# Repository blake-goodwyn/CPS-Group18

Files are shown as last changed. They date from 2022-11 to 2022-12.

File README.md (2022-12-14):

# CPS-Group18

## Overview

This is a repository for all development data regarding Group 18's work toward the Cyberphysical Systems module of the Imperial College London's Innovation Design Engineering (IDE) programme. The scope of this project is a 3-week design sprint aimed at a project of the students' choosing - in this case, developing a scale-model, soft-shelled Mars habitat structure that adjusts to aerodynamic shapes based on extreme wind patterns.  

The project team consists of:
- Abigail Hoover
- Richard Alexandre
- Richard "Blake" Goodwyn

## Working with these files

It is suggested that, due to the mechanism of how SolidWorks files are saved, anyone looking to work with the CAD files located in this repo either:
- place this repo at the C:/ location of their local machine
- open and re-save all SolidWorks once their environment has located the new file directory

This is an unfortunate side effect of mixing SolidWorks and Git, whereas an SVN system may be more appropriate. However, due to the fast-paced nature of this project and mixed media of its digital assets, GitHub seemed a reasonable solution for tracking development and hosting a final set of files.

## Mechanical Overview 
### (Refer to /cad folder)

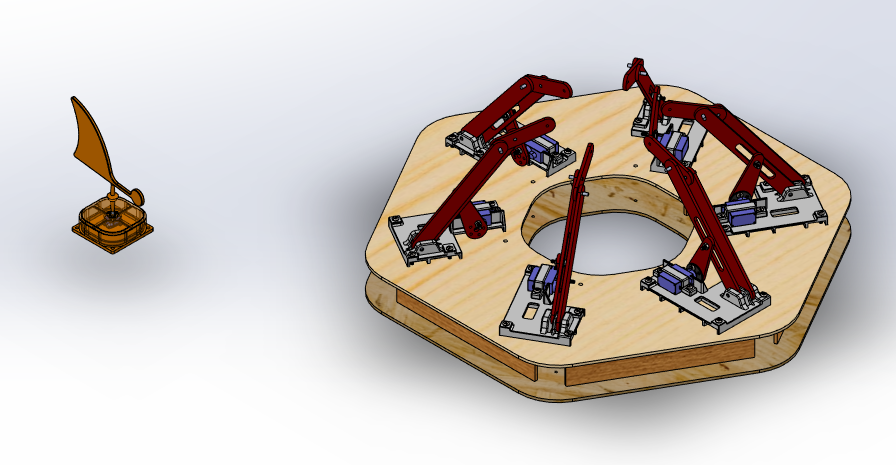
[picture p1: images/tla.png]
Top Level Assembly


The mechanical design of the structure consists of six mechanical arms spaced equally about the structure. Each one consists of a carefully developed 4-bar linkage system driven by a servo arm. The servo arm has a roller that is situated into a slot in a driving link and drives the tip of each arm up-and-down given the servo's position.

The mechanical design in this repo utilizes a top-down design ideology call **master modeling** to form all of the parts. Thus, the mechanical design is driven by three central files:
- *master.prt*, which contains critical assembly level design information like the structure's height and footprint
- *_submaster_linkage_module_4bar.prt*, which contains the critical design information for the assembly of each linkage module
- *_submaster_wind_vane.prt*, which contains the critical design information for the wind vane sub-assembly.

For more information on master modeling, you can refer to [this article from GoEngineer](https://www.goengineer.com/blog/solidworks-tutorial-master-modeling-technique).

## Software Overview
### (Refer to arduino_code)

Our software design utilises two core scripts in addition to a machine learning model to achieve its function: 
- an Arduino script (/arduino_code/MASTER_CODE/master_code) that handles motion of servos, packaging sensor inputs for the Wekinator module, 
and an interprets the feedback from the machine learning module
- a Processing script (machine_learning/master_processing_script/master_rx_tx_script) that takes in the analog sensor values from the Serial port and passes them to a Wekinator module
- a Wekinator machine learning module (machine_learning/final_ML_model/Finalized_ASH_ML_Model) that takes in 2 inputs in the form of float values and gives one integer output that denotes the class output of the model

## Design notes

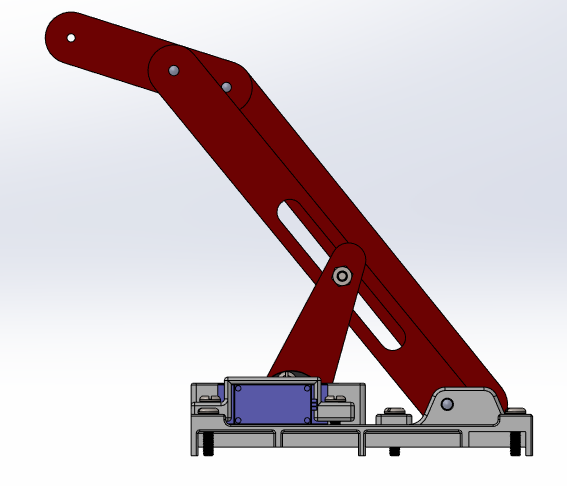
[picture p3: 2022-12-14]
images/linkage_subassy_right.png

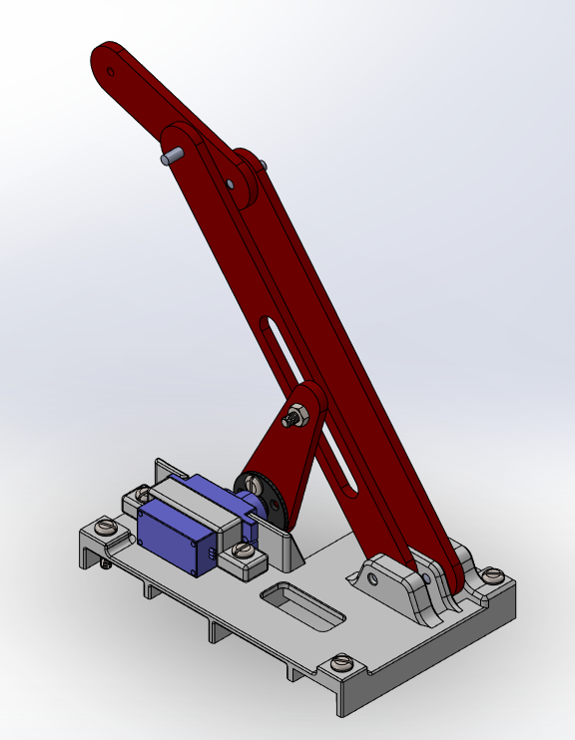
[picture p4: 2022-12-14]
images/linkage_subassy.png

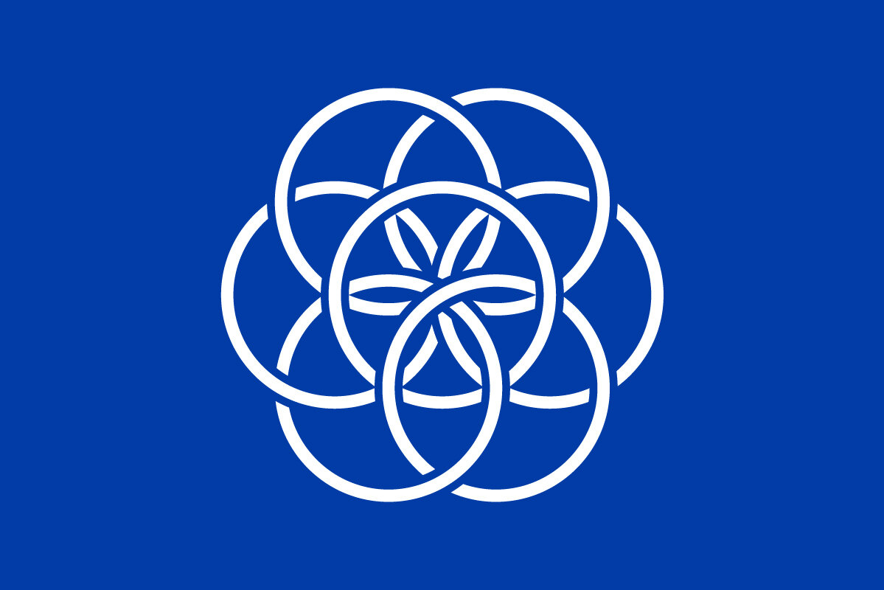
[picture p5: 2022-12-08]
images/EarthFlag.png

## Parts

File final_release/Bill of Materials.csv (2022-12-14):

PART NAME | QTY. | PROCESS | MATERIAL | VENDOR | SUPPLIER P/N | LINK | NOTES
windvane_housing | 1 | PRINT | PRUSA, 0.15MM PLA
wind_vane | 1 | PRINT | PRUSA, 0.15MM PLA
magnet_bracket | 1 | PRINT | PRUSA, 0.15MM PLA
pin_3mm_diam_12mm_length | 25 | PURCHASED | --- | RS COMPONENTS | 270-552 | https://uk.rs-online.com/web/p/dowel-pins/270552
round_bar_magnet | 1 | PURCHASED | --- | RS COMPONENTS | 536-1726 | https://uk.rs-online.com/web/p/magnets/5361726
wind_vane_base | 1 | PRINT | PRUSA, 0.15MM PLA
hall_effect_sensor_honeywell_SS495A | 2 | PURCHASED | --- | RS COMPONENTS | 216-6231 | https://uk.rs-online.com/web/p/hall-effect-sensors/2166231
washer_M3 | 13 | PURCHASED | --- | (STANDARD COMPONENT)
link1 | 6 | CUT | MDF, 3MM THK
link2 | 6 | CUT | MDF, 3MM THK
link3_slotted | 6 | CUT | MDF, 3MM THK
link4_servo_arm | 6 | CUT | MDF, 3MM THK
_mco_roller_link | 6 | PRINT | PRUSA, 0.15MM PLA
sg90 micro servo | 6 | PURCHASED | --- | Feetech | FS90MG
sg90_servo_wheel | 6 | PURCHASED | --- |  |  |  | (included with Feetech FS90MG)
servo_clamp | 6 | PRINT | PRUSA, 0.15MM PLA
servo_plate | 6 | PRINT | PRUSA, 0.15MM PLA
91200A118_18-8 Stainless Steel Pan Head Slotted Screw | 72 | PURCHASED | --- | (STANDARD COMPONENT) |  | https://www.mcmaster.com/91200A118/
91828A211_18-8 Stainless Steel Hex Nut | 48 | PURCHASED | --- | (STANDARD COMPONENT) |  | https://www.mcmaster.com/91828A211/
_new_base_top | 1 | CUT | MDF, 3MM THK
_new_base_bottom | 1 | CUT | MDF, 3MM THK
base_plate_rib | 6 | CUT | MDF, 3MM THK
base_plate_rib_outer | 6 | CUT | MDF, 3MM THK

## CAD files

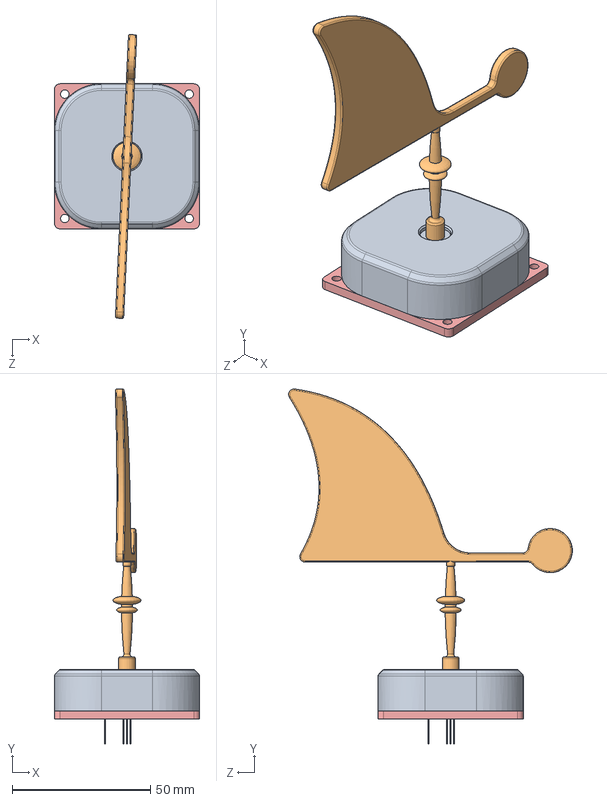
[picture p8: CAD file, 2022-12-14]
cad/_subassy_windvane.SLDASM
52.5 x 128.4 x 102.7 mm
windvane_housing
wind_vane
pin_3mm_diam_12mm_length
round_bar_magnet
wind_vane_base
hall_effect_sensor_honeywell_SS495A x 2
washer_M3

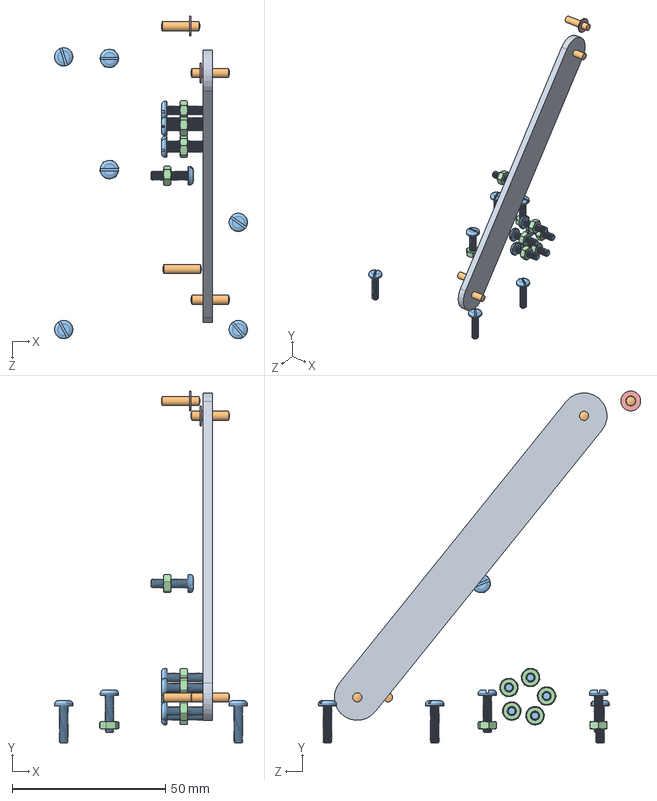
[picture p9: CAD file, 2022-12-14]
final_release/CAD/_subassy_linkage_module.SLDASM
63.0 x 114.9 x 105.3 mm
link1
pin_3mm_diam_12mm_length x 4
91200A118_18-8 Stainless Steel Pan Head Slotted Screws x 12
91828A211_18-8 Stainless Steel Hex Nut x 8
washer_M3 x 2

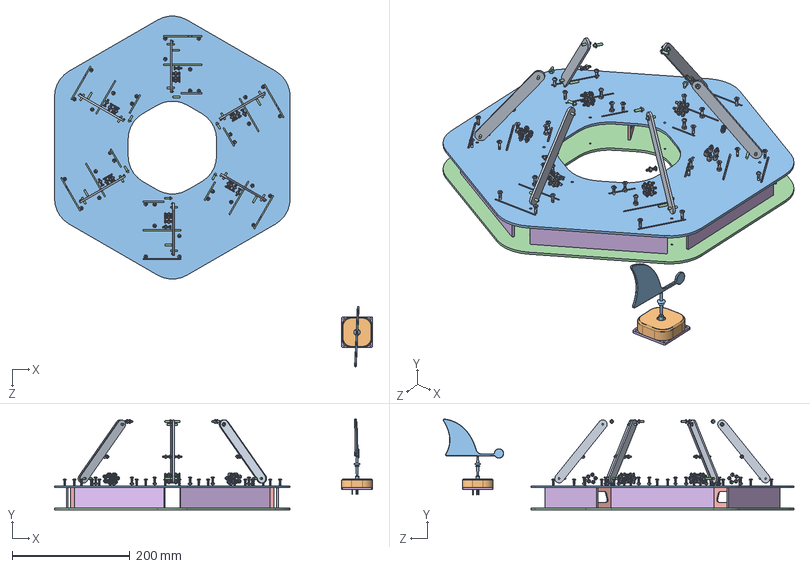
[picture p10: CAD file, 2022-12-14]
cad/_tla.SLDASM
539.6 x 154.4 x 595.0 mm
windvane_housing
wind_vane
pin_3mm_diam_12mm_length x 25
round_bar_magnet
wind_vane_base
hall_effect_sensor_honeywell_SS495A x 2
washer_M3 x 13
link1 x 6
91200A118_18-8 Stainless Steel Pan Head Slotted Screws x 72
91828A211_18-8 Stainless Steel Hex Nut x 48
_new_base_top
_new_base_bottom
base_plate_rib x 6
base_plate_rib_outer x 6

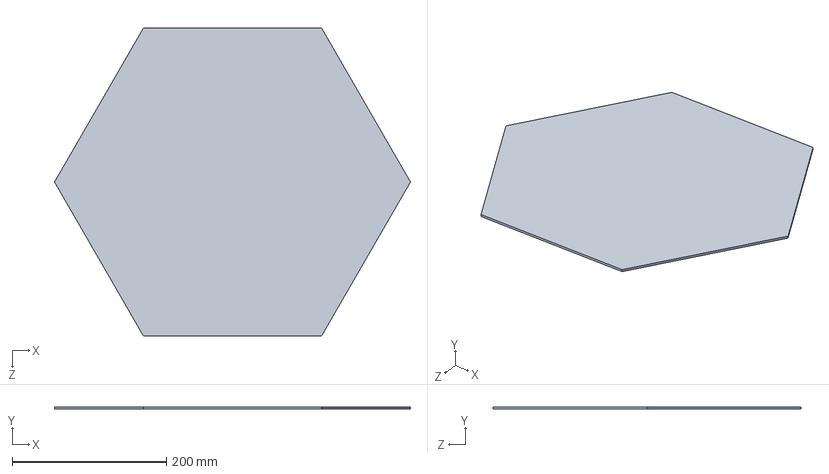
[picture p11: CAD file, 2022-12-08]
cad/_subassy_hexa_base.SLDASM
461.9 x 3.00 x 400.0 mm

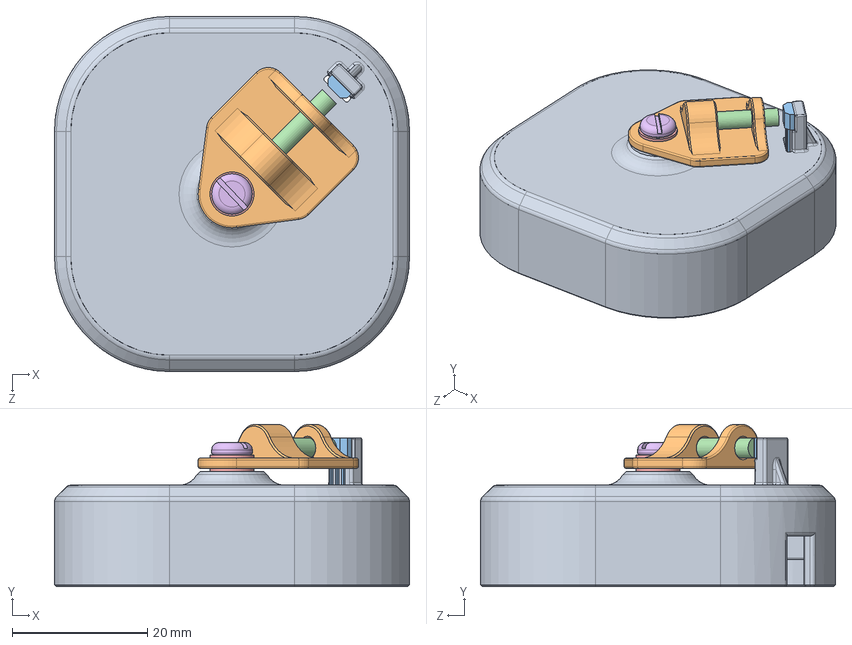
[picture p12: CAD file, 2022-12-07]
cad/_subassy_proto_windvane.SLDASM
52.5 x 24.0 x 52.5 mm
windvane_proto_housing
proto_accelerometer_plate
hall_effect_sensor_honeywell_SS495A
round_bar_magnet
washer_M3 x 3
91200A118_18-8 Stainless Steel Pan Head Slotted Screws
91828A211_18-8 Stainless Steel Hex Nut

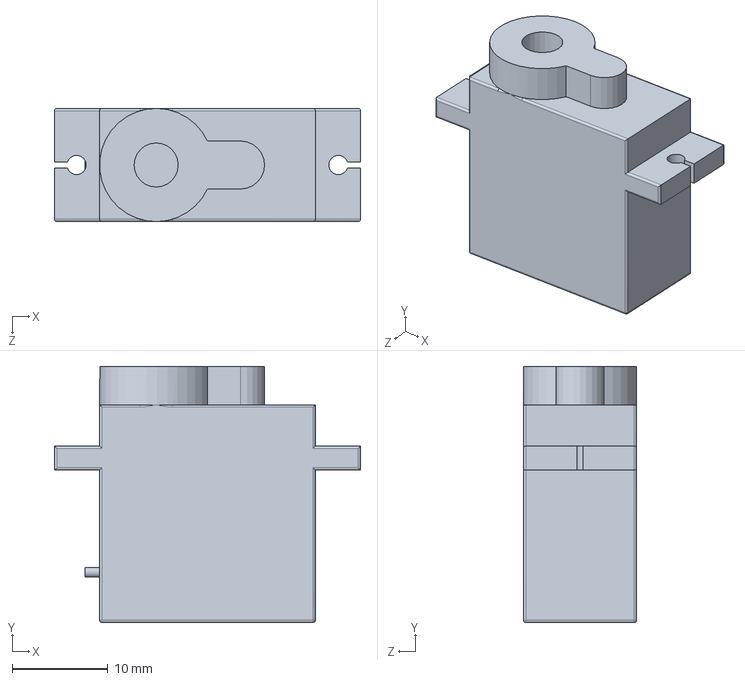
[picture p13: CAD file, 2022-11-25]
arduino_code/sg90-micro-servomotor-1.snapshot.2/Part1.SLDPRT
31.9 x 26.7 x 11.8 mm

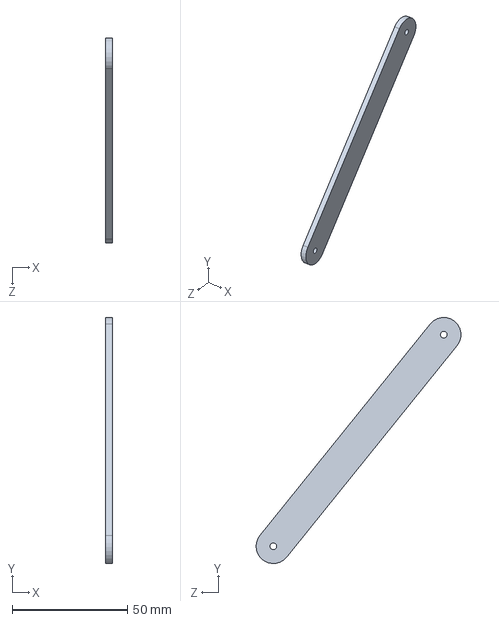
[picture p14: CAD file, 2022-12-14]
final_release/CAD/link1.SLDPRT
3.00 x 106.8 x 89.0 mm

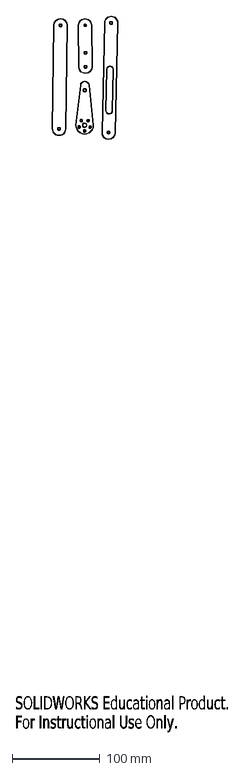
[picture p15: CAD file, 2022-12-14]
final_release/CUT/linkage_4bar_links_1set.DXF
SOLIDWORKS Educational Product.
For Instructional Use Only.

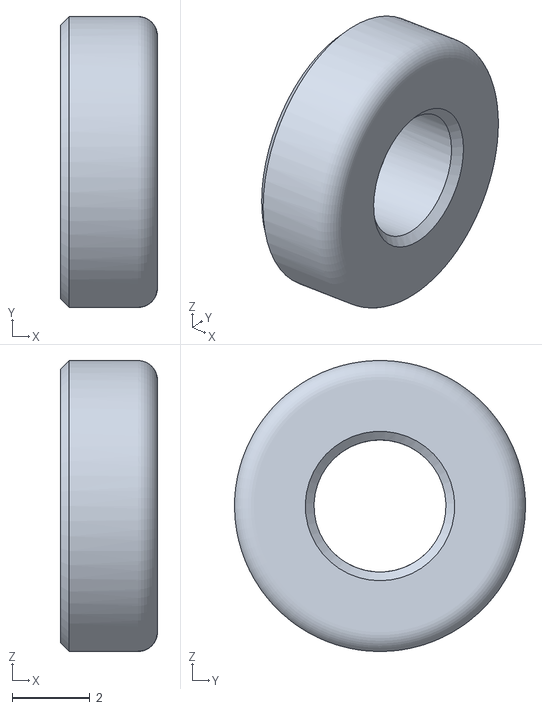
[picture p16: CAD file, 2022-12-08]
final_release/PRINT/roller_link.STL
2.50 x 7.50 x 7.50

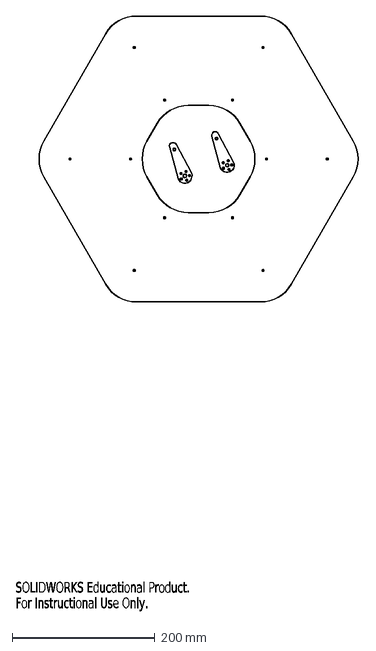
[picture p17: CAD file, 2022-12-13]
proto_releases/211213_base_cut/_new_base_bottom.DXF
SOLIDWORKS Educational Product.
For Instructional Use Only.

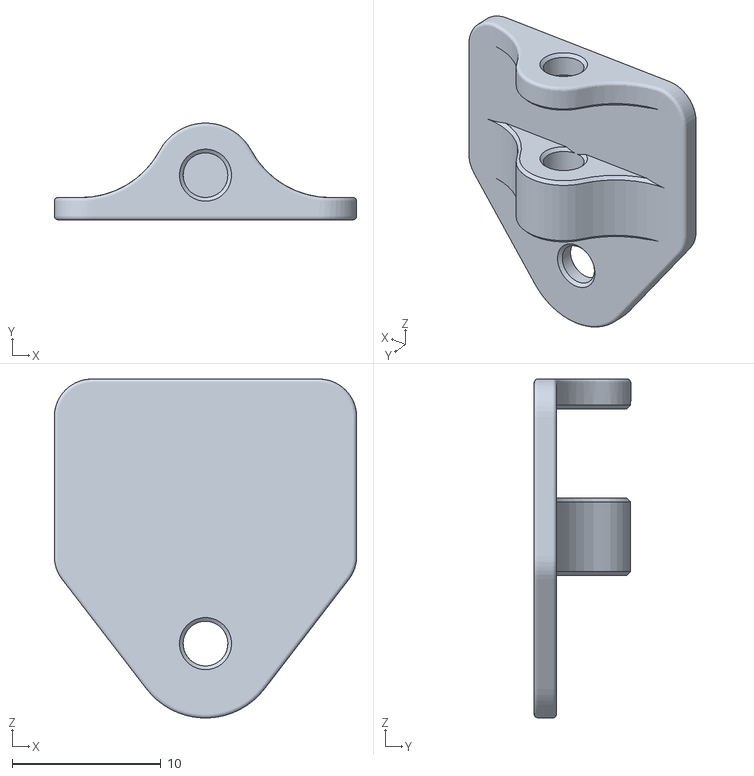
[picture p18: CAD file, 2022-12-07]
proto_releases/221202_windvane_sensor_proto_release/PRINT/proto_accelerometer_plate.STL
20.3 x 6.49 x 22.8

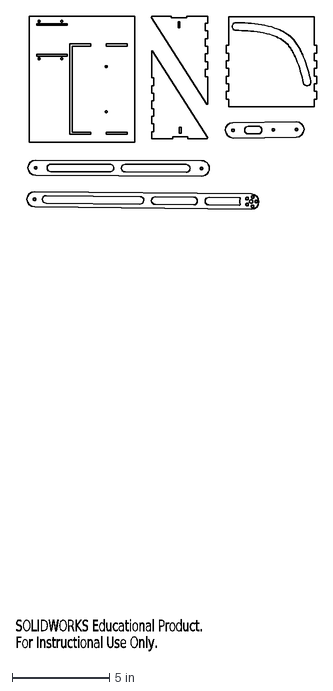
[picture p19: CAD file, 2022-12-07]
proto_releases/221206_linkage_proto_2_release/CUT/plate_linkage_mount.DXF
SOLIDWORKS Educational Product.
For Instructional Use Only.

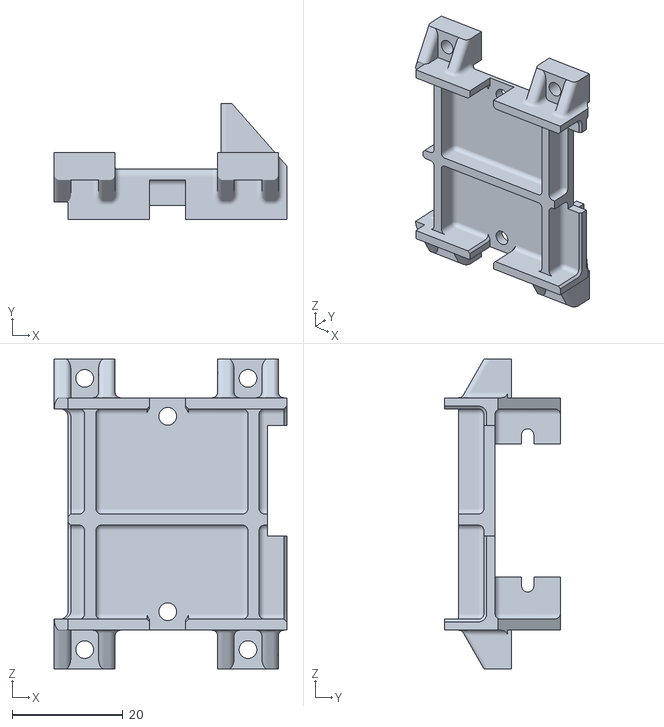
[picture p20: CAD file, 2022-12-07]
proto_releases/221206_linkage_proto_2_release/PRINT/servo_plate.STL
42.0 x 20.9 x 56.0

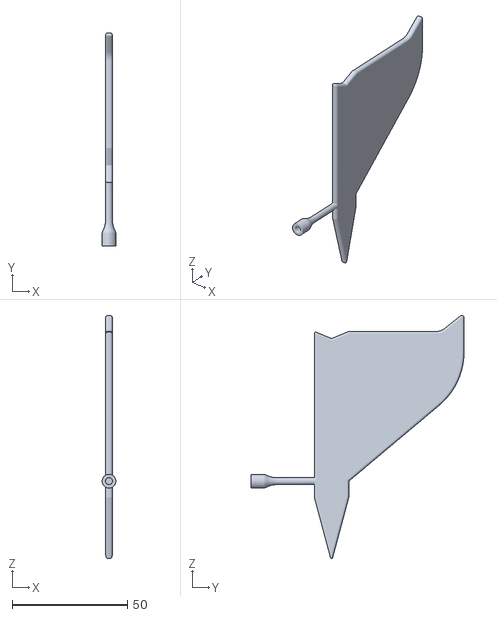
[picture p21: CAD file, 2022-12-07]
proto_releases/221207_windvane_sensor_proto_2_release/PRINT/wind_vane.STL
5.99 x 92.5 x 105.5

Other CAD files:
cad/_subassy_linkage_module.SLDASM
final_release/CAD/_subassy_windvane.SLDASM
final_release/CAD/_tla.SLDASM
proto_releases/221208_windvane_proto_3/PRINT/magnet_bracket.STL
arduino_code/sg90-micro-servomotor-1.snapshot.2/Part2.SLDPRT
arduino_code/sg90-micro-servomotor-1.snapshot.2/axis.STEP
arduino_code/sg90-micro-servomotor-1.snapshot.2/body.STEP
arduino_code/sg90-micro-servomotor-1.snapshot.2/sg90 micro servo.SLDASM
arduino_code/sg90-micro-servomotor-1.snapshot.2/sg90 micro servo.STEP
cad/221129_lasercut_linkage_prototype.SLDDRW
cad/221129_lasercut_linkage_prototype_2.SLDDRW
cad/91200A104_18-8 Stainless Steel Pan Head Slotted Screws.SLDPRT
cad/IGUS_M250_double_flange_bearing_MCM-03-03.SLDPRT
cad/Part3.SLDPRT
cad/Part4.SLDPRT
cad/_mco_roller_link.SLDPRT
cad/_new_base_bottom.SLDPRT
cad/_new_base_top.SLDPRT
cad/_submaster_linkage_module.SLDPRT
cad/_submaster_linkage_module_4bar.SLDPRT
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

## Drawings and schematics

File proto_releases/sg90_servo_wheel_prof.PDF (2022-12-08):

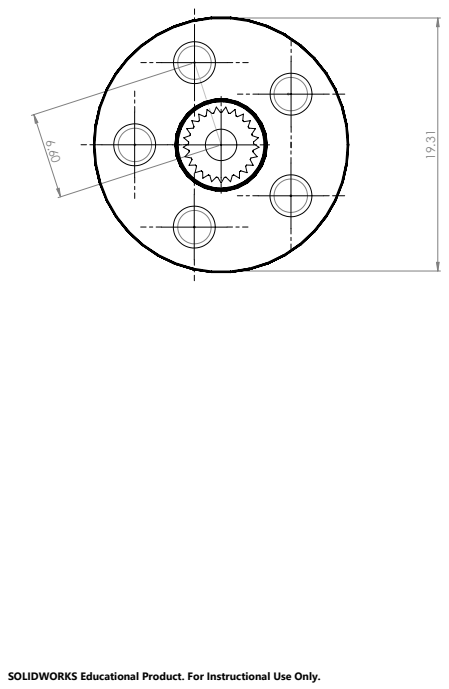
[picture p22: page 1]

SOLIDWORKS Educational Product. For Instructional Use Only.

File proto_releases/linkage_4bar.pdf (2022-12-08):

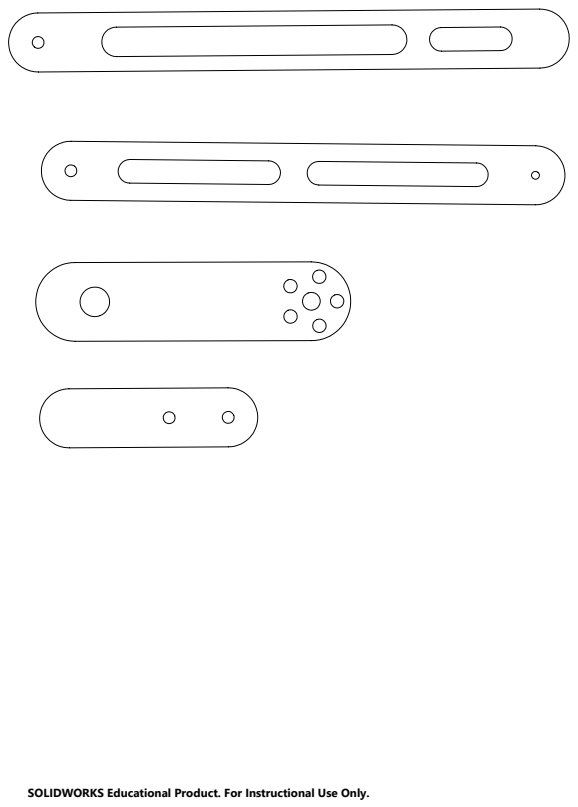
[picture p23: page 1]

SOLIDWORKS Educational Product. For Instructional Use Only.

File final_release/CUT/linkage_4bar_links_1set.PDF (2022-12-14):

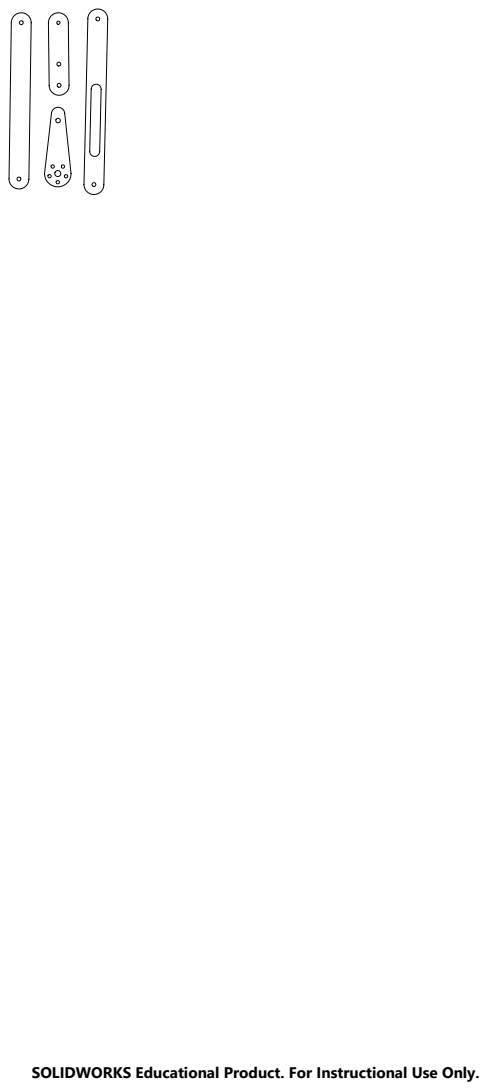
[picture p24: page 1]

SOLIDWORKS Educational Product. For Instructional Use Only.

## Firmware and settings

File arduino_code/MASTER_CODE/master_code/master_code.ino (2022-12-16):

/*  CPS GROUP 18 MASTER MOTION CODE
    Written by Blake Goodwyn, Abigail Hoover, and Richard Alexandre
    This Arduino script facilitates the core functions of the CPS project outcome, ASH, the Adjustable Space Hut.
    Core functions include:
    - Instantiating and managing software objects associated with mechanical arms
    - Encoding state machine model of structure and its transitions
    - Facilitating smoothed movement of mechanical arms per state machine transitions
    - Sending analog signals from Hall Effect sensors to Wekinator machine learning model
    - Decoding Wekinator machine learning model into state transitions
*/

#include "PCA9685.h"
#include <Wire.h>
#include "definitions.h"

/* Overview of function structure

SET_UP
1. Boot up
2. Set up one-time software objects

LOOP
3. Send analog signals from hall effect sensors to Wekinator
4. Interpret return signal from Wekinator
5. Transition to state and facilitate motion as needed 

*/

// --------------------------------------------------------

// -- INITIALIZATION --

//Instantiate Arm objects
Arm ArmA(arm_A_pin, sloper);
Arm ArmB(arm_B_pin, sloper);
Arm ArmC(arm_C_pin, sloper);
Arm ArmD(arm_D_pin, sloper);
Arm ArmE(arm_E_pin, sloper);
Arm ArmF(arm_F_pin, sloper);

//ServoDriver object contains all the code to drive the servos
ServoDriver servo;

//State signal from wekinator
int cur_MLstate = -1; //current ML state
int new_MLstate = -1; //new ML state

//Other variables
int c;                //global counter
bool cFlag = 0;       //motion flag

int timer1 = millis();
int timer2 = millis();

// --------------------------------------------------------

// FUNCTION DEFINITIONS

//Interpolate motions between start state and end state over set duration. Pushes interpolated motions to fixed array
void interpolateMotion(Arm *arm, int startDeg, int endDeg) {

  //Determine step size
  float step = (float(endDeg) - float(startDeg)) / (L - 1);

  //Populate array
  for (int i = 0; i < L; i++) {
    arm->setMove(((i * step) + startDeg), i);
  }
  #ifdef DEBUG
  Serial.println("Set Flag...");
  delay(DEBUG_delay);
  #endif
  arm->setFlag(1);
}

//Function to set arm position to defined angle
void armPosition(Arm *arm, int endState) {
  if(arm->getState() != endState){
    interpolateMotion(arm, arm->getState(), endState);
  }
}

//Function to broadcast analog read pins
void broadcast() {
  // read the input on analog pin 1:
  int sensorValue = analogRead(A1);
  Serial.print(sensorValue);

  sensorValue = analogRead(A2);
  Serial.print(", ");
  Serial.println(sensorValue);
}

//Function to receive and filter out incoming Wekinator messages
int receive(){
  
  String val;
  timer1 = millis();
  
  while (Serial.available() <= 0){
    
    //buffer statement
    Serial.println("waiting...");

    //timer condition to prevent hang up on broadcast calls
    timer2 = millis();
    if((timer2-timer1)>1000){
      return -1;
    }

  }
  val = Serial.readString(); // read it and store it in val
  
  #ifdef DEBUG
  //print received message
  Serial.print("<receive>: ");
  Serial.println(val);
  #endif
  
  //filter out Wekinator messages
  if(val.substring(0,2) == "RM"){
    
    #ifdef DEBUG
    Serial.println("Pass check");
    #endif

    int state = (val.substring(3)).toInt();

    #ifdef DEBUG
    Serial.println("State Transition!");
    Serial.println(state);
    #endif

    return state;

  }else{

    return -1;

  }
}

//Function to initialize serial contact with Processing script
void establishContact() {
  
  while (Serial.available() <= 0) {
    Serial.println("A");   // send a capital A as generic single-char confirmation
    delay(300);
  }
}

//Function to encode state machine transitions as interpreted by incoming signals from Wekinator
void stateTransition(int state) {
  
  switch(state){
    case 1:
    #ifdef DEBUG
      Serial.println("Case: threeSixty");
      delay(DEBUG_delay);
    #endif
      armPosition(&ArmA, crimp);
      armPosition(&ArmB, crimp);
      armPosition(&ArmC, normal);
      armPosition(&ArmD, sloper);
      armPosition(&ArmE, sloper);
      armPosition(&ArmF, normal);
      break;
  case 2:
    #ifdef DEBUG
      Serial.println("Case: sixty");
      delay(DEBUG_delay);
    #endif
      armPosition(&ArmA, normal);
      armPosition(&ArmB, crimp);
      armPosition(&ArmC, crimp);
      armPosition(&ArmD, normal);
      armPosition(&ArmE, sloper);
      armPosition(&ArmF, sloper);
      break;
  case 3:
    #ifdef DEBUG
      Serial.println("Case: oneTwenty");
      delay(DEBUG_delay);
    #endif
      armPosition(&ArmA, sloper);
      armPosition(&ArmB, normal);
      armPosition(&ArmC, crimp);
      armPosition(&ArmD, crimp);
      armPosition(&ArmE, normal);
      armPosition(&ArmF, sloper);
      break;
  case 4:
    #ifdef DEBUG
      Serial.println("Case: oneEighty");
      delay(DEBUG_delay);
    #endif
      armPosition(&ArmA, sloper);
      armPosition(&ArmB, sloper);
      armPosition(&ArmC, normal);
      armPosition(&ArmD, crimp);
      armPosition(&ArmE, crimp);
      armPosition(&ArmF, normal);
      break;
  case 5:
    #ifdef DEBUG
      Serial.println("Case: twoForty");
      delay(DEBUG_delay);
    #endif
      armPosition(&ArmA, normal);
      armPosition(&ArmB, sloper);
      armPosition(&ArmC, sloper);
      armPosition(&ArmD, normal);
      armPosition(&ArmE, crimp);
      armPosition(&ArmF, crimp);
      break;
  case 6: 
    #ifdef DEBUG
      Serial.println("Case: threeHundred");
      delay(DEBUG_delay);
    #endif
      armPosition(&ArmA, crimp);
      armPosition(&ArmB, normal);
      armPosition(&ArmC, sloper);
      armPosition(&ArmD, sloper);
      armPosition(&ArmE, normal);
      armPosition(&ArmF, crimp);
      break;
  case 7:
    #ifdef DEBUG
      Serial.println("Case: defDirection");
      delay(DEBUG_delay);
    #endif
      armPosition(&ArmA, normal);
      armPosition(&ArmB, normal);
      armPosition(&ArmC, normal);
      armPosition(&ArmD, normal);
      armPosition(&ArmE, normal);
      armPosition(&ArmF, normal);
      break;
  case 8:
    #ifdef DEBUG
      Serial.println("Case: defDirection");
      delay(DEBUG_delay);
    #endif
      armPosition(&ArmA, crimp);
      armPosition(&ArmB, crimp);
      armPosition(&ArmC, crimp);
      armPosition(&ArmD, crimp);
      armPosition(&ArmE, crimp);
      armPosition(&ArmF, crimp);
      break;
  }
}

// --------------------------------------------------------

// ONE-TIME SETUP

void setup() {

  // spin up I2C bus for motor shield comms.
  Wire.begin();
  
  // spin up serial bus
  Serial.begin(9600);
  
  //initialize servo comms.
  servo.init(0x7f);

  #ifdef DEBUG
  Serial.println("");
  Serial.println("");
  Serial.println("--- SETUP START ---");
  delay(DEBUG_delay);
  #endif

  //move arms from sloper position (initialized) to default positions
  #ifdef DEBUG
  Serial.println("Default Positions");
  delay(DEBUG_delay);
  #endif

  cur_MLstate = 7;
  stateTransition(cur_MLstate);

  //reach out to Processing to establish common Serial connection
  #ifndef DUMMY_INPUT
  establishContact();
  #endif
}

// --------------------------------------------------------

// MASTER LOOP FUNCTION

void loop() {
  
  #ifdef DEBUG
  Serial.println("--- LOOP START ---");
  delay(DEBUG_delay);
  #endif

  #ifdef DEBUG
  Serial.println("Broadcast...");
  delay(DEBUG_delay);
  #endif

  // LOOP STEP 1 - Broadcast latest analog signals
  broadcast();

  // LOOP STEP 2 - Queue up motion if valid transition is provided
  #ifdef DUMMY_INPUT

  // dummy input branch for testing state transitions without machine learning input
  if(cFlag == 0){
    #ifdef DEBUG
    Serial.println("Dummy serial input...");
    delay(DEBUG_delay);
    #endif
    while (Serial.available() == 0){
      void;
    }
    new_MLstate = Serial.parseInt();
    #ifdef DEBUG
    Serial.print("MLstate: ");
    Serial.println(int(new_MLstate));
    #endif
    stateTransition(new_MLstate);
  };
  #else

  // branch for real-time state transitions
  if (cFlag == 0){
    #ifndef TRAIN //if defined, provides no state transitions but outputs signals for training
    new_MLstate = receive();
    if((new_MLstate != -1) && (new_MLstate != cur_MLstate)){
      stateTransition(new_MLstate);
      cur_MLstate = new_MLstate;
      #ifdef DEBUG
      Serial.print("State: ");
      Serial.println(cur_MLstate);
      #endif
    }
    #endif
  }
  #endif

  // LOOP STEP 3 - increment all designated arm positions per loaded motion profiles
  
  // define global motion flag
  cFlag = ArmA.getFlag() || ArmB.getFlag() || ArmC.getFlag() || ArmD.getFlag() || ArmE.getFlag() || ArmF.getFlag();
  
  if (cFlag) {
    
    #ifdef DEBUG
    Serial.print("Increment: ");
    Serial.println(c);
    delay(DEBUG_delay);
    #endif

    if (ArmA.getFlag()) {
      #ifdef DEBUG
      Serial.print("Arm A Move: ");
      Serial.println(ArmA.getMove(c));
      delay(DEBUG_delay);
      #endif
      servo.setAngle(ArmA.getPin(), ArmA.getMove(c)+A_OFFSET);
    }
    if (ArmB.getFlag()) {
      #ifdef DEBUG
      Serial.print("Arm B Move: ");
      Serial.println(ArmB.getMove(c));
      delay(DEBUG_delay);
      #endif
      servo.setAngle(ArmB.getPin(), ArmB.getMove(c)+B_OFFSET);
    }
    if (ArmC.getFlag()) {
      #ifdef DEBUG
      Serial.print("Arm C Move: ");
      Serial.println(ArmC.getMove(c));
      delay(DEBUG_delay);
      #endif
      servo.setAngle(ArmC.getPin(), ArmC.getMove(c)+C_OFFSET);
    }
    if (ArmD.getFlag()) {
      #ifdef DEBUG
      Serial.print("Arm D Move: ");
      Serial.println(ArmD.getMove(c));
      delay(DEBUG_delay);
      #endif
      servo.setAngle(ArmD.getPin(), ArmD.getMove(c)+D_OFFSET);
    }
    if (ArmE.getFlag()) {
      #ifdef DEBUG
      Serial.print("Arm E Move: ");
      Serial.println(ArmE.getMove(c));
      delay(DEBUG_delay);
      #endif
      servo.setAngle(ArmE.getPin(), ArmE.getMove(c)+E_OFFSET);
    }
    if (ArmF.getFlag()) {
      #ifdef DEBUG
      Serial.print("Arm F Move: ");
      Serial.println(ArmF.getMove(c));
      delay(DEBUG_delay);
      #endif
      servo.setAngle(ArmF.getPin(), ArmF.getMove(c)+F_OFFSET);
    }

    c++;            //increment global counter
    if (c >= L) {   //if global counter reaches end of arrays

      #ifdef DEBUG
      Serial.println("// End of Movement //");
      delay(DEBUG_delay);
      #endif

      //store current state in Arm objects
      ArmA.setState(ArmA.getMove(c-1));
      ArmB.setState(ArmB.getMove(c-1));
      ArmC.setState(ArmC.getMove(c-1));
      ArmD.setState(ArmD.getMove(c-1));
      ArmE.setState(ArmE.getMove(c-1));
      ArmF.setState(ArmF.getMove(c-1));

      //set all move flags to FALSE
      ArmA.setFlag(0);
      ArmB.setFlag(0);
      ArmC.setFlag(0);
      ArmD.setFlag(0);
      ArmE.setFlag(0);
      ArmF.setFlag(0);

      //reset global counter
      c = 0;
    }
  }
  delay(delayStep);
  #ifdef DEBUG
  Serial.println("--- LOOP END ---");
  delay(DEBUG_delay); 
  #endif
}

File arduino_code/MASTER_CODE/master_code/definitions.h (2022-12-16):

/*  DEFINITIONS.h
    This is a header file containing relevant constants and definitions for operation of the master_code.ino script
*/

#ifndef definitions_h
#define definitions_h
#define DEBUG_delay 50

//DEBUGGING DEFINITIONS
//#define DEBUG
#undef DEBUG

#undef TEST_SWEEP       //test sweep tag
//#define DUMMY_INPUT   //dummy input tag
//#define TRAIN

// BIG LENGTH 
// Defines the resolution of the arm movements
#ifdef DEBUG
  #define L 15
#else if
  #define L 50
#endif
//**this is a tradeoff between motion resolution AND file size (more res, more size)

//Motion Parameters
int duration = 500; //ms
int delayStep = duration/L;

// Arms Pin Positions on Motor Shield
#define arm_A_pin 2
#define arm_B_pin 16
#define arm_C_pin 9
#define arm_D_pin 12
#define arm_E_pin 5
#define arm_F_pin 4

// Arm States
#define sloper 90
#define crimp 200
#define normal 150

// Arm Position Trimming
#define A_OFFSET -10
#define B_OFFSET 0
#define C_OFFSET 0
#define D_OFFSET 0
#define E_OFFSET 35
#define F_OFFSET -10

//Class definition for mechanical arm object
class Arm
{
  public:
    Arm::Arm(int pin, int state);
    int getState();
    void setState(int state);
    int getPin();
    int getMove(int i);
    void setMove(int val, int i);
    bool getFlag();
    void setFlag(bool flag);

  private:
    int _curState;
    int _pinPosition;
    int _moveArray[L];
    bool _moveFlag;
};

//Object instantiation function
Arm::Arm(int pin, int state){
  
  _curState = state;
  _pinPosition = pin;
  _moveFlag = 0;
  for(int i = 0; i < L; i++){
    _moveArray[i] = _curState;
  }

}

//getter function for Arm pin position on motor shield
int Arm::getPin(){
  return _pinPosition;
}

//getter function for current stored Arm position
int Arm::getState(){
  return _curState;
}

//setter function for current stored Arm position
void Arm::setState(int state){
  _curState = state;
}

//getter function for motion flag
bool Arm::getFlag(){
  return _moveFlag;
}

//setter function for motion flag
void Arm::setFlag(bool flag){
  _moveFlag = flag;
};

//getter function for element of motion array
int Arm::getMove(int i){
  return _moveArray[i];
};

//setter function for element of motion array
void Arm::setMove(int val, int i){
  _moveArray[i] = val;
}

#endif

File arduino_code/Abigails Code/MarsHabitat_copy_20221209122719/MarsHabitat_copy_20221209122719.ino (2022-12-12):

/* 
Cyber Physcials 2022/23 GID/IDE
Mars Habitat 
By: Abigail Hoover, Blake Goodwyn, Richard Alexandre 

This script features connecting and checking both servos and hall effect senors. 
Gathering voltages of Hall Effect sensors and running it through wekinator then outputing
a specific state to move our habitat 
*/

// Libraries //
#include "definitions.h"
#include "PCA9685.h"

// Properties // 
char ssid[] = "yourNetwork"; // your network SSID (name) 
char pass[] = "12345678"; // your network password
int status = WL_IDLE_STATUS; // the Wifi radio's status


void setup() {
  // initialise serial:
  Serial.begin(9600);
}


// the loop routine runs over and over again forever:
void loop() {
  // read the input on analog pin 0:
  int sensorValue = analogRead(A0);
  // print out the value you read:
  Serial.println(sensorValue);
  int sensorValue = analogRead(A1);
  Serial.println(sensorValue);
  int sensorValue = analogRead(A2);
  Serial.println(sensorValue);
  int sensorValue = analogRead(A3);
  Serial.println(sensorValue);
  delay(1);  // delay in between reads for stability
}

// Turns values into OSC and send to wekinator 
// Get state from wekinator 

// Servo Cases //
void loop() {
  // read the sensor:
  if (Serial.available() > 0) {
    int inByte = Serial.read();
    // do something different depending on the character received.
    // The switch statement expects single number values for each case;
    // in this exmaple, though, you're using single quotes to tell
    // the controller to get the ASCII value for the character.  For
    // example 'a' = 97, 'b' = 98, and so forth:

void arm_position (int arm, int endstates) {
   servo.setAngle(arm, endstate);
}

// define state 

switch (state) {
  case "360deg":
    arm_position(arm_A, crimp);
    arm_position(arm_B, crimp);
    arm_position(arm_C, normal);
    arm_position(arm_D, sloper);
    arm_position(arm_E, sloper);
    arm_position(arm_F, normal);
    break;
  case "60deg":
    arm_position(arm_A, normal);
    arm_position(arm_B, crimp);
    arm_position(arm_C, crimp);
    arm_position(arm_D, normal);
    arm_position(arm_E, sloper);
    arm_position(arm_F, sloper);
    break;
  case "120deg":
    arm_position(arm_A, sloper);
    arm_position(arm_B, normal);
    arm_position(arm_C, crimp);
    arm_position(arm_D, crimp);
    arm_position(arm_E, normal);
    arm_position(arm_F, sloper);
    break;
  case "180deg":
    arm_position(arm_A, sloper);
    arm_position(arm_B, sloper);
    arm_position(arm_C, normal);
    arm_position(arm_D, crimp);
    arm_position(arm_E, crimp);
    arm_position(arm_F, normal);
    break;
  case "240deg":
    arm_position(arm_A, normal);
    arm_position(arm_B, sloper);
    arm_position(arm_C, sloper);
    arm_position(arm_D, normal);
    arm_position(arm_E, crimp);
    arm_position(arm_F, crimp);
    break;
  case "300deg":
    arm_position(arm_A, crimp);
    arm_position(arm_B, normal);
    arm_position(arm_C, sloper);
    arm_position(arm_D, sloper);
    arm_position(arm_E, normal);
    arm_position(arm_F, crimp);
    break;
  default:
    arm_position(arm_A, normal);
    arm_position(arm_B, normal);
    arm_position(arm_C, normal);
    arm_position(arm_D, normal);
    arm_position(arm_E, normal);
    arm_position(arm_F, normal);
    break;
  }
}

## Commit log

2022-11-25 initial model files
    The initial commit!
    Includes:
    - initial master model of footprint
    - initial submaster model of linkage system
    - placeholder servo model
    - initial top-level assembly with servo placement
    [Part1.SLDPRT, Part2.SLDPRT, _master.SLDPRT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]
2022-11-25 added tla
    added top level assembly file
    added rough part for clip bearings
    [IGUS_M250_double_flange_bearing_MCM-03-03.SLDPRT, _submaster_linkage_module.SLDPRT, _tla.SLDASM]
2022-11-25 update to submaster_linkage
    added potential constraint path to linkage part
    [_submaster_linkage_module.SLDPRT]
2022-11-28 windvane refinement
    added parts for windvane design
    [_master.SLDPRT, _subassy_windvane.SLDASM, _submaster_linkage_module.SLDPRT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]
2022-11-29 linkage prototype
    added linkage parts for prototyping
    [_mco_roller_link.SLDPRT, _subassy_linkage_module.SLDASM, _submaster_linkage_module.SLDPRT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]
2022-11-29 linkage module prototype
    refined linkage module subassembly prototype for lasercutting and 3D printing
    [_mco_roller_link.SLDPRT, _subassy_linkage_module.SLDASM, _submaster_linkage_module.SLDPRT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]
2022-11-29 rotated linkage prototype
    rotated so it's easier to lasercut parts!
    [91200A104_18-8 Stainless Steel Pan Head Slotted Screws.SLDPRT, 91200A118_18-8 Stainless Steel Pan Head Slotted Screws.SLDPRT, _master.SLDPRT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]
2022-11-29 generated prototype release files
    [221129_lasercut_linkage_prototype.DXF, 221129_lasercut_linkage_prototype.SLDDRW, 221129_lasercut_linkage_prototype_2.DXF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]
2022-11-29 further refinements on prototype release
    -added consistent (available) fasteners and parts to support them
    -consolidated material props
    [221129_PRUSA_EXPORT.3mf, 221129_lasercut_linkage_prototype.DXF, 221129_lasercut_linkage_prototype.SLDDRW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]
2022-11-30 finalized proto release (actually this time)
    some tweaks and detailing
    [221129_PRUSA_EXPORT.3mf, 221129_lasercut_linkage_prototype.DXF, 221129_lasercut_linkage_prototype.SLDDRW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]
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2022-12-02 creat branch / init release files for vane proto
    refined windvane sensor set-up for testing and potential training data
    [_subassy_proto_windvane.SLDASM, _submaster_wind_vane.SLDPRT, hall_effect_sensor_honeywell_SS495A.SLDPRT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]
2022-12-04 added proto release files
    proto release files for printing on morning on 12/5, ahead of receiving parts
    [221202_sensing_proto_arrangement.3mf]
2022-12-05 05122022
    Fucking around with Spline line for curvature of path in track plate
    [_mco_roller_link.SLDPRT, _subassy_linkage_module.SLDASM, _submaster_linkage_module.SLDPRT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]
2022-12-06 incorporated changes on main linkage assembly
    manual merge of changes from abigail's and richard's branches
    [_master.SLDPRT, _mco_roller_link.SLDPRT, _subassy_linkage_module.SLDASM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]
2022-12-06 some DFM changes before iteration 2 cut
    [_mco_roller_link.SLDPRT, _subassy_linkage_module.SLDASM, _submaster_linkage_module.SLDPRT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]
2022-12-06 staging proto 2 STL files
    [_mco_roller_link.STL, brace_track_plate.STL, servo_clamp.STL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]
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2022-12-06 downsized & added 4bar variant
    -downsized the _tla to 40cm from 80cm (and other parts accordingly)
    -sketched a 4bar linkage concept for potential dev
    [221206_Blake_Goodwyn_Proto_2.3mf, _master.SLDPRT, _mco_roller_link.SLDPRT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]
2022-12-07 refinements from hall effect testing
    [_subassy_windvane.SLDASM, _submaster_wind_vane.SLDPRT, accelerometer_plate.SLDPRT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]
2022-12-07 windvane proto 2 release
    [_subassy_windvane.SLDASM, _submaster_wind_vane.SLDPRT, accelerometer_plate.SLDPRT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]
2022-12-07 fixing merge bugs
    [_tla.SLDASM]
2022-12-08 08122022
    Messing around with links
    [_master.SLDPRT, _submaster_linkage_module_4bar.SLDPRT, linkage_4bar_Link1.SLDPRT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]
2022-12-08 commit before pull of 4bar work
    [Part3.SLDPRT, Part4.SLDPRT, _mco_roller_link.SLDPRT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]
2022-12-08 Abigail Commited this to our branch
    Linkage changes
    [_submaster_linkage_module_4bar.SLDPRT]
2022-12-08 Idk tons of stuff
    idk tons of stuff
    [_submaster_linkage_module_4bar.SLDPRT, _submaster_wind_vane.SLDPRT, linkage_4bar.DXF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]
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2022-12-08 WE GOT AN ASSEMBLY OVER HERE
    [_mco_roller_link.SLDPRT, _new_base.SLDPRT, _new_base_bottom.SLDPRT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]
2022-12-08 finalizing linkage proto 3 layout
    it's lookin' pretty darn good if I do write so myself
    [_master.SLDPRT, _mco_roller_link.SLDPRT, _new_base_bottom.SLDPRT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]
2022-12-08 staged release files for linkage proto3
    [221209_Blake_Goodwyn_linkage3_proto.3mf, 221209_linkage3_5_Sets_layout.DXF, 221209_linkage3_5_Sets_layout.SLDDRW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]
2022-12-09 more release files and changed to existing ones
    pin fits, pin fits, pin fits
    [221209_linkage3_5_Sets_layout.DXF, 221209_linkage3_5_Sets_layout.SLDDRW, 221209_linkage3_layout.SLDDRW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]
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2022-12-13 pushing multiple changes
    bottom base cut
    new tla
    new code
    [221213_new_base_bottom.DXF, _master.SLDPRT, _mco_roller_link.SLDPRT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]
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
